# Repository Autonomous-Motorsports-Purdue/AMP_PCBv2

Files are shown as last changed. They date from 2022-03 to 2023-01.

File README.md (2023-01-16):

# AMP PCB version 2

This PCB attempts to refine the v1 PCB to strip away extraneous components and achieve the best minimal set of components needed for drive, steering, and braking control

## Features

| Name | Current Status | Notes |
|---|---|---|
| Foot switch | Working | Master enable for motor controller
| Forward throttle | Working | -
| Reverse throttle | Working | -
| Motor brake control | Untested | Primary braking system if working
| Emergency brake control | Working | Mechanical brake actuator
| Steering | Working | 0-100% PWM duty cycle control
| LoRa remote control | Partially tested | -
| Watchdog timer | Broken on Rev A | -
| Hardware serial port | Working | -

---

## Technical Information
- [Teensy 4.0 front pinout](docs/img/Teensy_40_Front_Pinout.png)
- [Teensy 4.0 rear pinout](docs/img/Teensy_40_Rear_Pinout.png)
- [Emergency brake controller truth table](docs/img/Brake_Control_Signals.png)

### Useful links
- [RC Low-pass Filter Design for PWM](http://sim.okawa-denshi.jp/en/PWMtool.php)
- [Software setup for Teensy with Arduino](https://www.pjrc.com/teensy/tutorial.html)

---

## Part Numbers
| Part Number | Description |
|---|---|
| [776164-1](https://www.digikey.com/en/products/detail/te-connectivity-deutsch-ict-connectors/776164-1/2183727) | AMPSEAL (main motor controller connector) 35-pin connector
| [770520-1](https://www.digikey.com/en/products/detail/te-connectivity-amp-connectors/770520-1/744981) | AMPSEAL crimps

---

## Miscellaneous notes (to check)

- Create documentation for connectors (especially motor controller connector)
- Create complete BOM for PCB

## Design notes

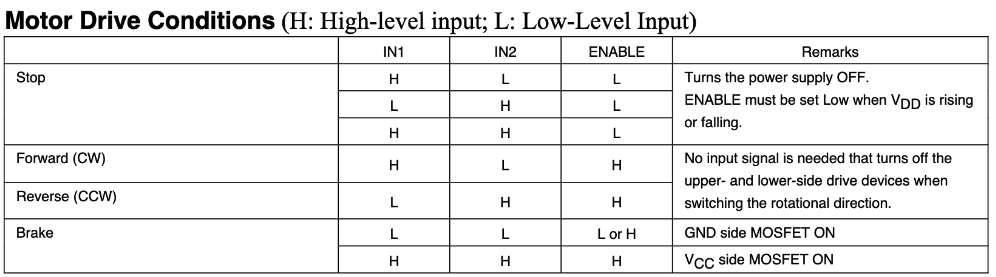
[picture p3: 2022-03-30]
docs/img/Brake_Control_Signals.png

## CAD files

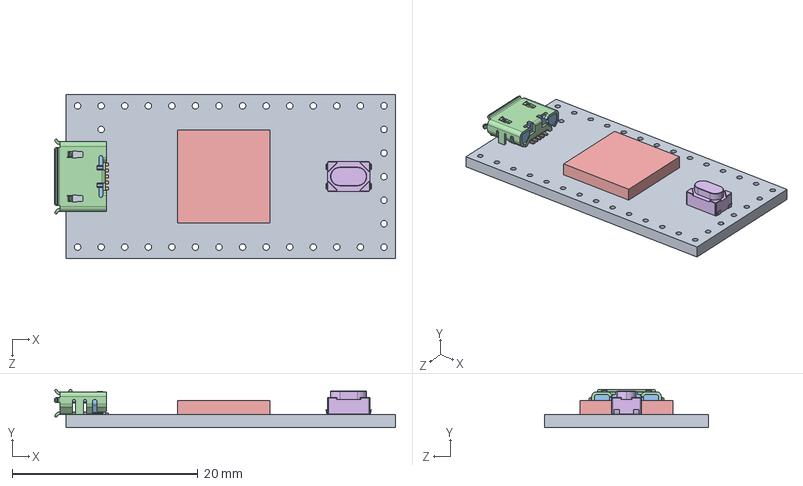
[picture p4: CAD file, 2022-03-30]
footprints/models/Teensy_4.0_Assembly.STEP
36.8 x 4.12 x 17.7 mm
Teensy_4.0_PCB
Micro USB-B Female 5Pin SMD
NXP iMXRT1062
SKRPACE010 v4

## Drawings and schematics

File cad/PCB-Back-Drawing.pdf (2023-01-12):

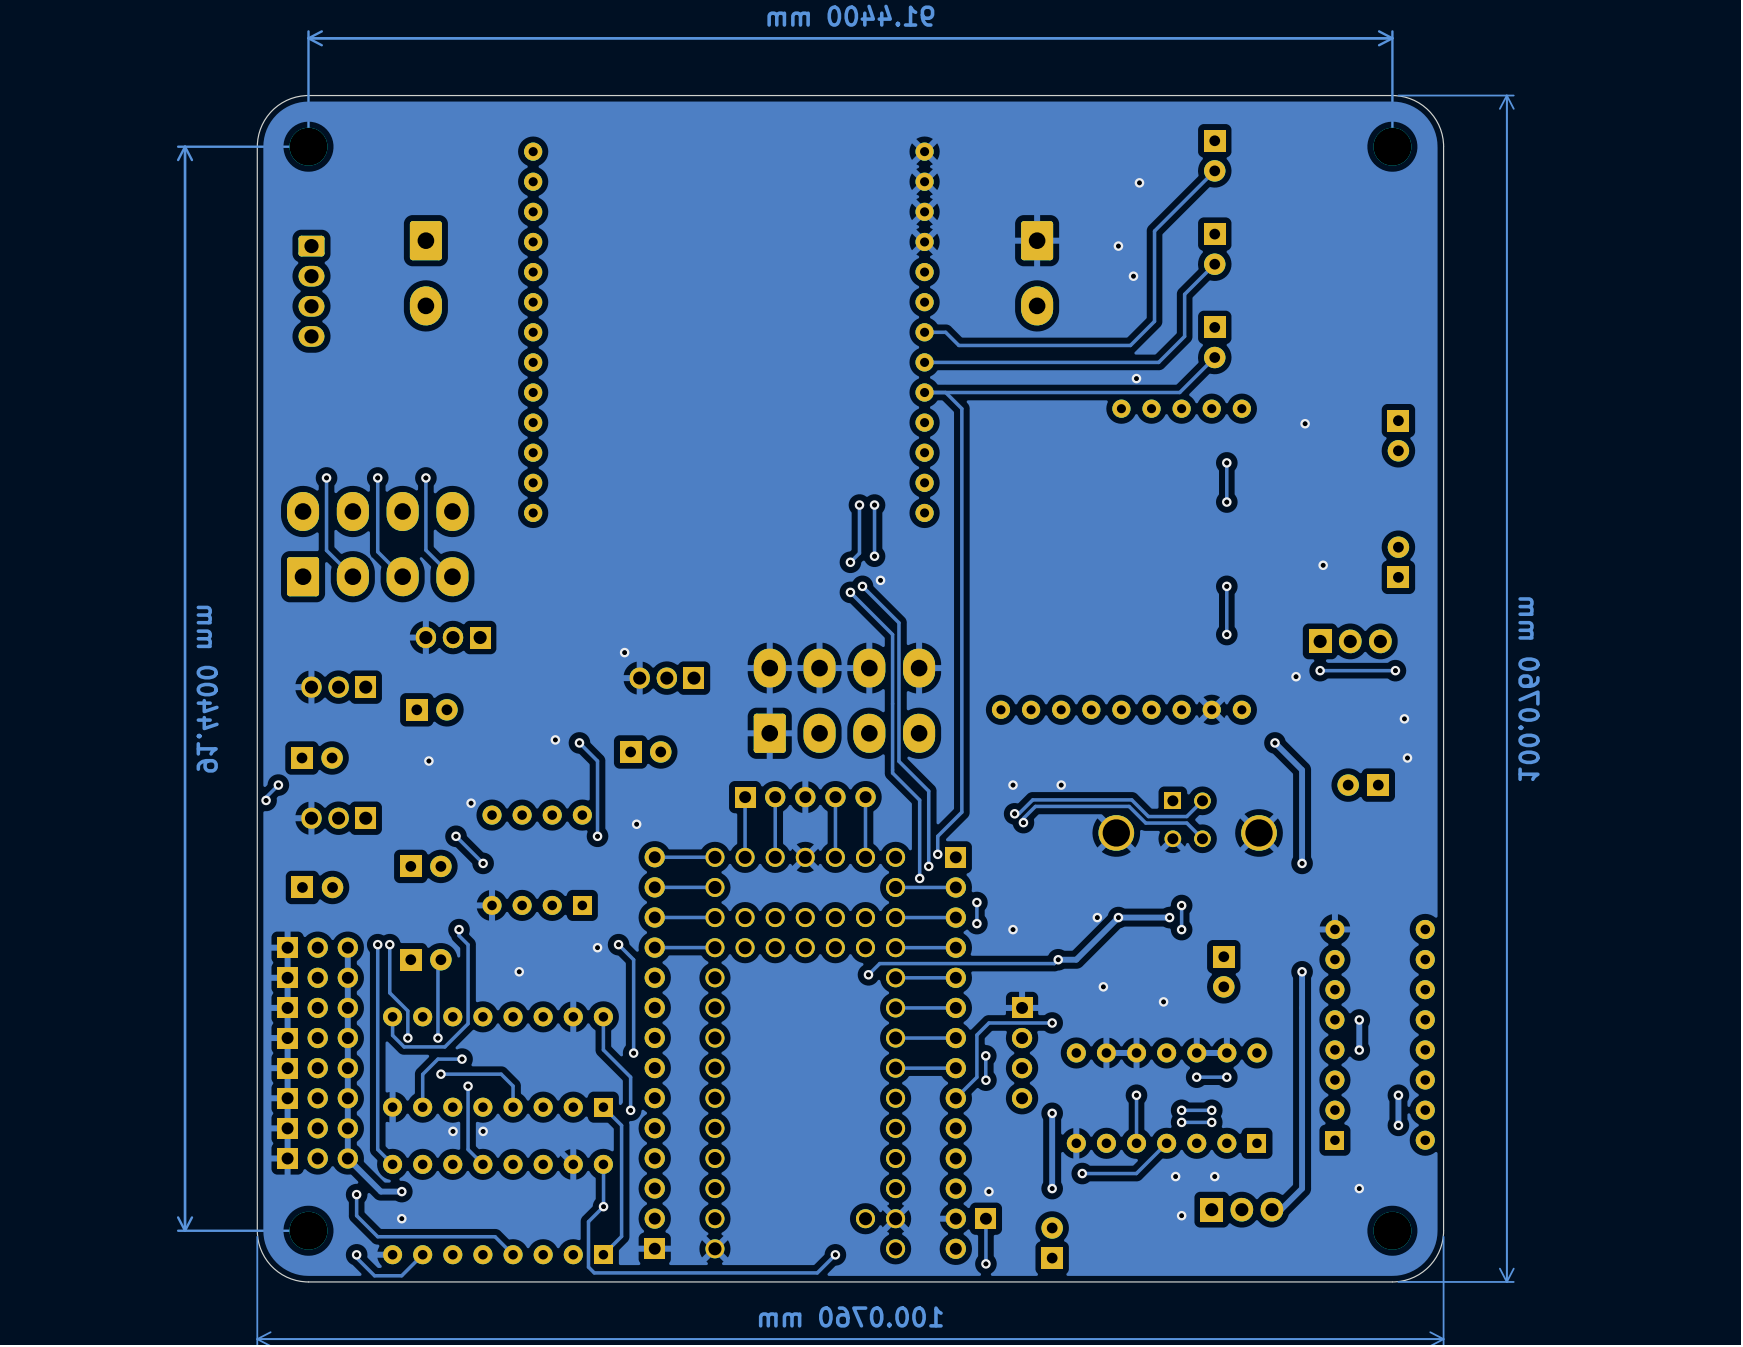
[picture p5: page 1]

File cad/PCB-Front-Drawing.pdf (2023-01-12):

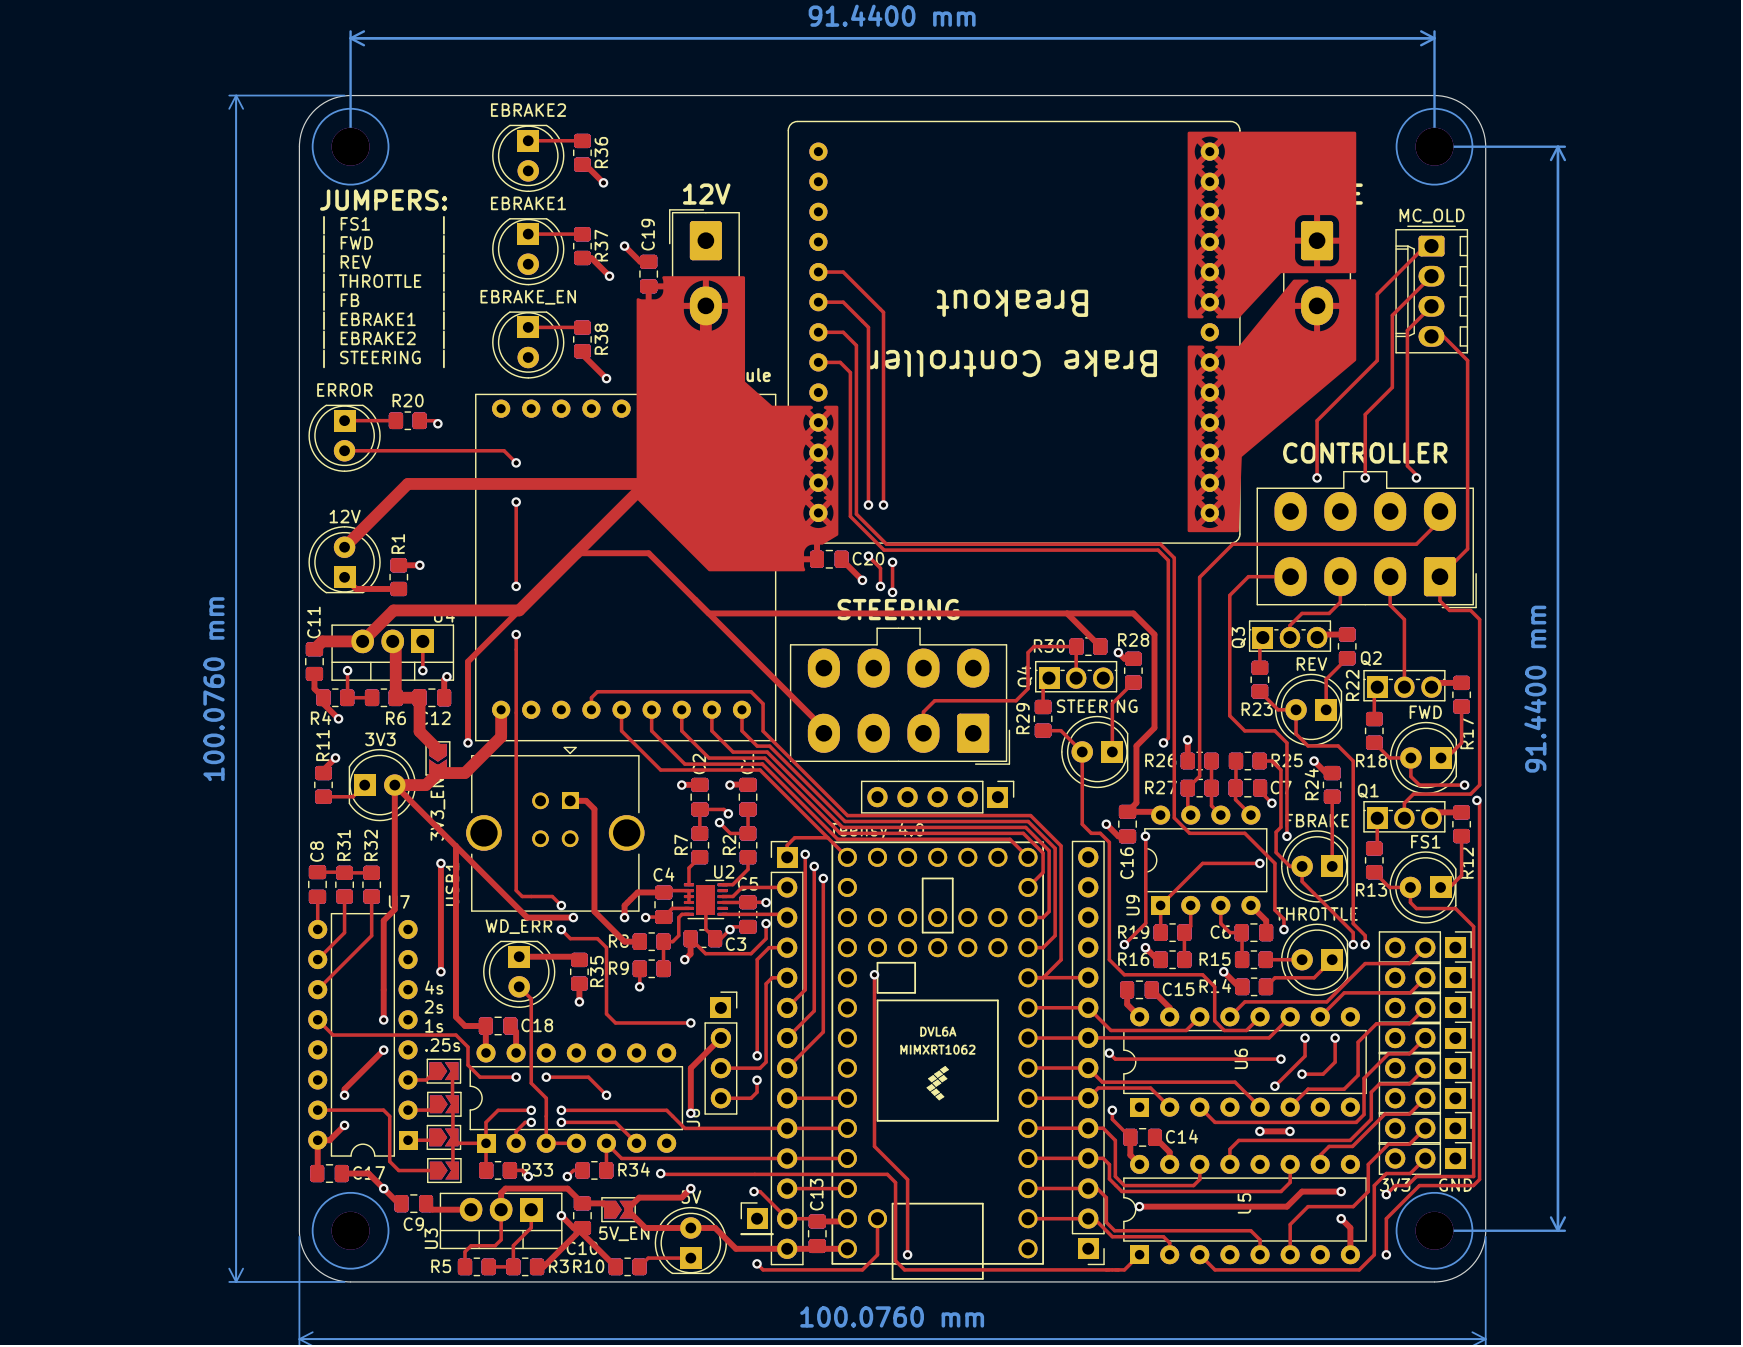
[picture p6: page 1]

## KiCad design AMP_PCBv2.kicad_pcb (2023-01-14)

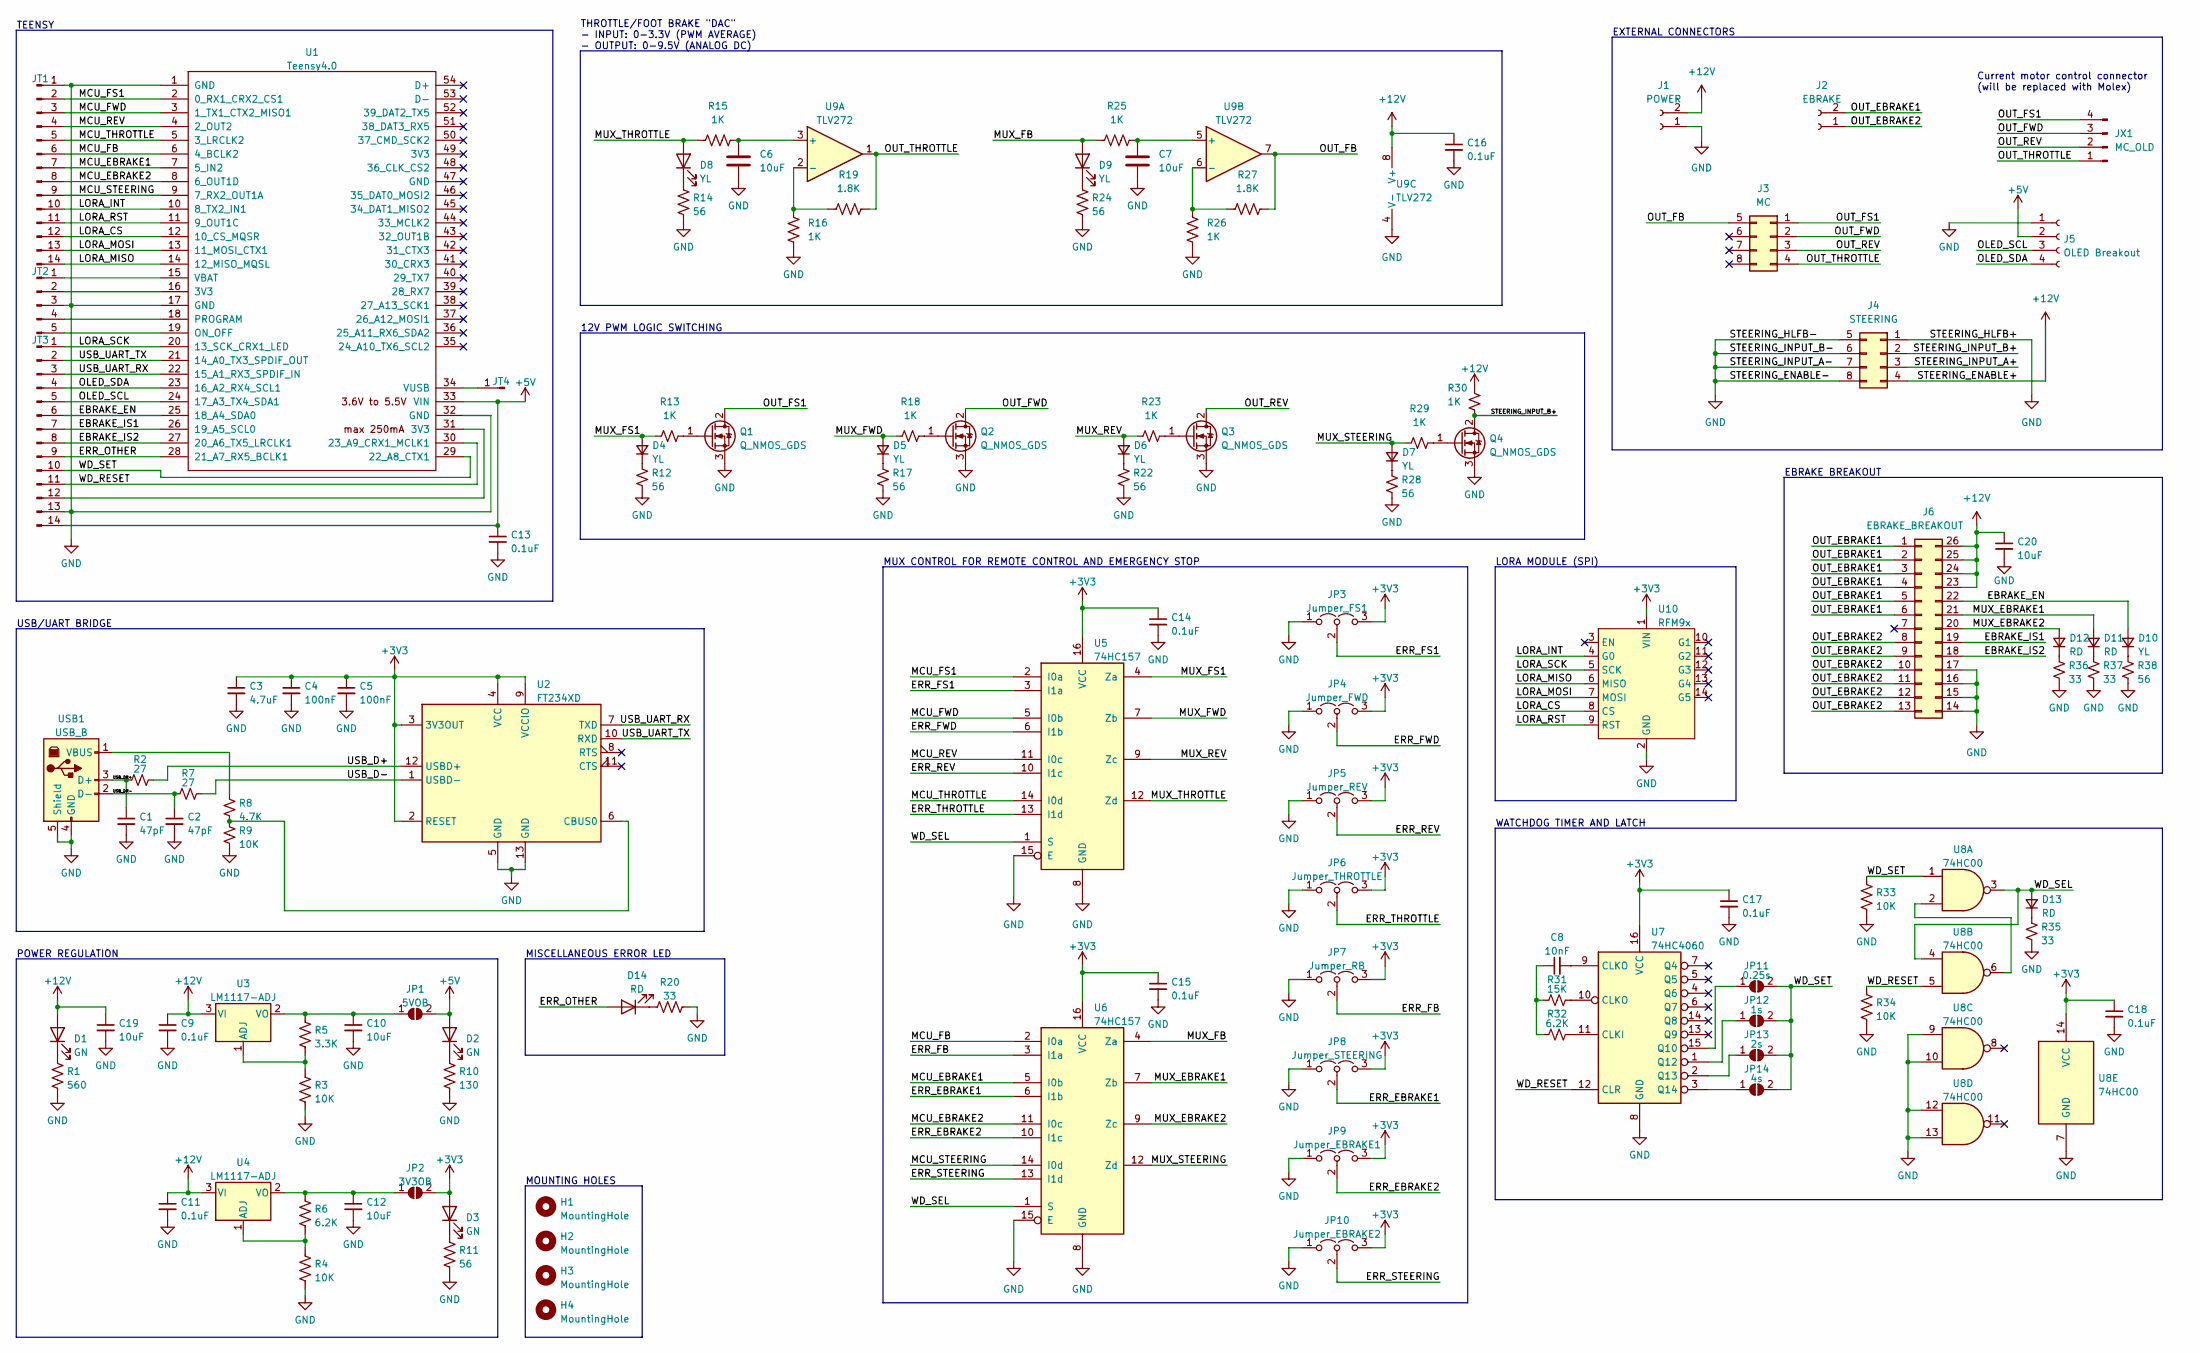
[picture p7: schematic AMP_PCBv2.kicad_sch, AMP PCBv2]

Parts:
C1, C2: 47pF; C_0805_2012Metric_Pad1.18x1.45mm_HandSolder
C3: 4.7uF; C_0805_2012Metric_Pad1.18x1.45mm_HandSolder
C4, C5: 100nF; C_0805_2012Metric_Pad1.18x1.45mm_HandSolder
C6, C7, C10, C12, C19, C20: 10uF; C_0805_2012Metric_Pad1.18x1.45mm_HandSolder
C8: 10nF; C_0805_2012Metric_Pad1.18x1.45mm_HandSolder
C9, C11, C13, C14, C15, C16, C17, C18: 0.1uF; C_0805_2012Metric_Pad1.18x1.45mm_HandSolder
D1, D2, D3: GN; LED_D5.0mm
D4, D5, D6, D7, D8, D9, D10: YL; LED_D5.0mm
D11, D12, D13, D14: RD; LED_D5.0mm
H1, H2, H3, H4: MountingHole; MountingHole_3.2mm_M3
J1: POWER; Molex_Mini-Fit_Jr_5566-02A_2x01_P4.20mm_Vertical
J2: EBRAKE; Molex_Mini-Fit_Jr_5566-02A_2x01_P4.20mm_Vertical
J3: MC; Molex_Mini-Fit_Jr_5566-08A_2x04_P4.20mm_Vertical
J4: STEERING; Molex_Mini-Fit_Jr_5566-08A_2x04_P4.20mm_Vertical
J5: OLED Breakout; PinSocket_1x04_P2.54mm_Vertical
J6: EBRAKE_BREAKOUT; AMP_Brake_Controller_Breakout
JP1: 5VOB; SolderJumper-2_P1.3mm_Open_TrianglePad1.0x1.5mm
JP2: 3V3OB; SolderJumper-2_P1.3mm_Open_TrianglePad1.0x1.5mm
JP3: Jumper_FS1; PinHeader_1x03_P2.54mm_Vertical
JP4: Jumper_FWD; PinHeader_1x03_P2.54mm_Vertical
JP5: Jumper_REV; PinHeader_1x03_P2.54mm_Vertical
JP6: Jumper_THROTTLE; PinHeader_1x03_P2.54mm_Vertical
JP7: Jumper_RB; PinHeader_1x03_P2.54mm_Vertical
JP8: Jumper_STEERING; PinHeader_1x03_P2.54mm_Vertical
JP9: Jumper_EBRAKE1; PinHeader_1x03_P2.54mm_Vertical
JP10: Jumper_EBRAKE2; PinHeader_1x03_P2.54mm_Vertical
JP11: 0.25s; SolderJumper-2_P1.3mm_Open_TrianglePad1.0x1.5mm
JP12: 1s; SolderJumper-2_P1.3mm_Open_TrianglePad1.0x1.5mm
JP13: 2s; SolderJumper-2_P1.3mm_Open_TrianglePad1.0x1.5mm
JP14: 4s; SolderJumper-2_P1.3mm_Open_TrianglePad1.0x1.5mm
JT1, JT3: Conn_01x14_Male; PinHeader_1x14_P2.54mm_Vertical
JT2: Conn_01x05_Male; PinHeader_1x05_P2.54mm_Vertical
JT4: Conn_01x01_Male; PinHeader_1x01_P2.54mm_Vertical
JX1: MC_OLD; Molex_KK-254_AE-6410-04A_1x04_P2.54mm_Vertical
Q1, Q2, Q3, Q4: Q_NMOS_GDS; TO-251-3_Vertical
R1: 560; R_0805_2012Metric_Pad1.20x1.40mm_HandSolder
R2, R7: 27; R_0805_2012Metric_Pad1.20x1.40mm_HandSolder
R3, R4, R9, R33, R34: 10K; R_0805_2012Metric_Pad1.20x1.40mm_HandSolder
R5: 3.3K; R_0805_2012Metric_Pad1.20x1.40mm_HandSolder
R6, R32: 6.2K; R_0805_2012Metric_Pad1.20x1.40mm_HandSolder
R8: 4.7K; R_0805_2012Metric_Pad1.20x1.40mm_HandSolder
R10: 130; R_0805_2012Metric_Pad1.20x1.40mm_HandSolder
R11, R12, R14, R17, R22, R24, R28, R38: 56; R_0805_2012Metric_Pad1.20x1.40mm_HandSolder
R13, R15, R16, R18, R23, R25, R26, R29, R30: 1K; R_0805_2012Metric_Pad1.20x1.40mm_HandSolder
R19, R27: 1.8K; R_0805_2012Metric_Pad1.20x1.40mm_HandSolder
R20, R35, R36, R37: 33; R_0805_2012Metric_Pad1.20x1.40mm_HandSolder
R31: 15K; R_0805_2012Metric_Pad1.20x1.40mm_HandSolder
U1: Teensy4.0; Teensy40
U2: FT234XD; DFN-12-1EP_3x3mm_P0.5mm_EP1.6x2.5mm
U3, U4: LM1117-ADJ; TO-220-3_Vertical
U5, U6: 74HC157; DIP-16_W7.62mm
U7: 74HC4060; DIP-16_W7.62mm
U8: 74HC00; DIP-14_W7.62mm
U9: TLV272; DIP-8_W7.62mm
U10: RFM9x; RFM9x_Adafruit
USB1: USB_B; USB_B_TE_5787834_Vertical

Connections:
+3V3: C3.1, C4.1, C5.1, C14.1, C15.1, C17.1, C18.1, D3.2 (A), JP2.2 (B), JP3.3 (B), JP4.3 (B), JP5.3 (B), JP6.3 (B), JP7.3 (B), JP8.3 (B), JP9.3 (B), JP10.3 (B), U2.2 (RESET), U2.3 (3V3OUT), U2.4 (VCC), U2.9 (VCCIO), U5.16 (VCC), U6.16 (VCC), U7.16 (VCC), U8.14 (VCC), U10.1 (VIN)
+5V: C13.1, D2.2 (A), J5.2, JP1.2 (B), JT3.14, U1.33 (VIN)
+12V: C9.1, C11.1, C16.1, C19.1, C20.1, D1.2 (A), J1.2, J4.4, J6.23, J6.24, J6.25, J6.26, R30.2, U3.3 (VI), U4.3 (VI), U9.8 (V+)
/EBRAKE_EN: D10.2 (A), J6.22, JT3.6, U1.25 (18_A4_SDA0)
/EBRAKE_IS1: J6.19, JT3.7, U1.26 (19_A5_SCL0)
/EBRAKE_IS2: J6.18, JT3.8, U1.27 (20_A6_TX5_LRCLK1)
/ERR_EBRAKE1: JP8.2 (C), U6.6 (I1b)
/ERR_EBRAKE2: JP9.2 (C), U6.10 (I1c)
/ERR_FB: JP7.2 (C), U6.3 (I1a)
/ERR_FS1: JP3.2 (C), U5.3 (I1a)
/ERR_FWD: JP4.2 (C), U5.6 (I1b)
/ERR_OTHER: D14.2 (A), JT3.9, U1.28 (21_A7_RX5_BCLK1)
/ERR_REV: JP5.2 (C), U5.10 (I1c)
/ERR_STEERING: JP10.2 (C), U6.13 (I1d)
/ERR_THROTTLE: JP6.2 (C), U5.13 (I1d)
/LORA_CS: JT1.12, U1.12 (10_CS_MQSR), U10.8 (CS)
/LORA_INT: JT1.10, U1.10 (8_TX2_IN1), U10.4 (G0)
/LORA_MISO: JT1.14, U1.14 (12_MISO_MQSL), U10.6 (MISO)
/LORA_MOSI: JT1.13, U1.13 (11_MOSI_CTX1), U10.7 (MOSI)
/LORA_RST: JT1.11, U1.11 (9_OUT1C), U10.9 (RST)
/LORA_SCK: JT3.1, U1.20 (13_SCK_CRX1_LED), U10.5 (SCK)
/MCU_EBRAKE1: JT1.7, U1.7 (5_IN2), U6.5 (I0b)
/MCU_EBRAKE2: JT1.8, U1.8 (6_OUT1D), U6.11 (I0c)
/MCU_FB: JT1.6, U1.6 (4_BCLK2), U6.2 (I0a)
/MCU_FS1: JT1.2, U1.2 (0_RX1_CRX2_CS1), U5.2 (I0a)
/MCU_FWD: JT1.3, U1.3 (1_TX1_CTX2_MISO1), U5.5 (I0b)
/MCU_REV: JT1.4, U1.4 (2_OUT2), U5.11 (I0c)
/MCU_STEERING: JT1.9, U1.9 (7_RX2_OUT1A), U6.14 (I0d)
/MCU_THROTTLE: JT1.5, U1.5 (3_LRCLK2), U5.14 (I0d)
/MUX_EBRAKE1: D11.2 (A), J6.21, U6.7 (Zb)
/MUX_EBRAKE2: D12.2 (A), J6.20, U6.9 (Zc)
/MUX_FB: D9.2 (A), R25.1, U6.4 (Za)
/MUX_FS1: D4.2 (A), R13.1, U5.4 (Za)
/MUX_FWD: D5.2 (A), R18.1, U5.7 (Zb)
/MUX_REV: D6.2 (A), R23.1, U5.9 (Zc)
/MUX_STEERING: D7.2 (A), R29.1, U6.12 (Zd)
/MUX_THROTTLE: D8.2 (A), R15.1, U5.12 (Zd)
/OLED_SCL: J5.3, JT3.5, U1.24 (17_A3_TX4_SDA1)
/OLED_SDA: J5.4, JT3.4, U1.23 (16_A2_RX4_SCL1)
/OUT_EBRAKE1: J2.2, J6.1, J6.2, J6.3, J6.4, J6.5, J6.6
/OUT_EBRAKE2: J2.1, J6.8, J6.9, J6.10, J6.11, J6.12, J6.13
/OUT_FB: J3.5, R27.2, U9.7
/OUT_FS1: J3.1, JX1.4, Q1.2 (D)
/OUT_FWD: J3.2, JX1.3, Q2.2 (D)
/OUT_REV: J3.3, JX1.2, Q3.2 (D)
/OUT_THROTTLE: J3.4, JX1.1, R19.2, U9.1
/STEERING_INPUT_A+: J4.3
/STEERING_INPUT_B+: J4.2, Q4.2 (D), R30.1
/USB_D+: R2.2, U2.12 (USBD+)
/USB_D-: R7.2, U2.1 (USBD-)
/USB_DR+: C1.1, R2.1, USB1.3 (D+)
/USB_DR-: C2.1, R7.1, USB1.2 (D-)
/USB_UART_RX: JT3.3, U1.22 (15_A1_RX3_SPDIF_IN), U2.7 (TXD)
/USB_UART_TX: JT3.2, U1.21 (14_A0_TX3_SPDIF_OUT), U2.10 (RXD)
/WD_RESET: JT3.11, R34.1, U1.30 (23_A9_CRX1_MCLK1), U7.12 (CLR), U8.5
/WD_SEL: D13.2 (A), U5.1 (S), U6.1 (S), U8.3, U8.4
/WD_SET: JP11.2 (B), JP12.2 (B), JP13.2 (B), JP14.2 (B), JT3.10, R33.1, U1.29 (22_A8_CTX1), U8.1
GND: C1.2, C2.2, C3.2, C4.2, C5.2, C6.2, C7.2, C9.2, C10.2, C11.2, C12.2, C13.2, C14.2, C15.2, C16.2, C17.2, C18.2, C19.2, C20.2, J1.1, J4.1, J4.5, J4.6, J4.7, J4.8, J5.1, J6.14, J6.15, J6.16, J6.17, JP3.1 (A), JP4.1 (A), JP5.1 (A), JP6.1 (A), JP7.1 (A), JP8.1 (A), JP9.1 (A), JP10.1 (A), JT1.1, JT2.3, JT3.13, Q1.3 (S), Q2.3 (S), Q3.3 (S), Q4.3 (S), R1.2, R3.1, R4.1, R9.2, R10.2, R11.2, R12.2, R14.2, R16.2, R17.2, R20.2, R22.2, R24.2, R26.2, R28.2, R33.2, R34.2, R35.2, R36.2, R37.2, R38.2, U1.1 (GND), U1.17 (GND), U1.32 (GND), U2.5 (GND), U2.13 (GND), U5.8 (GND), U5.15 (E), U6.8 (GND), U6.15 (E), U7.8 (GND), U8.7 (GND), U8.9, U8.10, U8.12, U8.13, U9.4 (V-), U10.2 (GND), USB1.4 (GND), USB1.5 (Shield)
unnamed: C6.1, R15.2, U9.3 (+)
unnamed: C7.1, R25.2, U9.5 (+)
unnamed: C8.1, R31.1, R32.1
unnamed: C8.2, U7.9 (CLKO)
unnamed: C10.1, JP1.1 (A), R5.1, U3.2 (VO)
unnamed: C12.1, JP2.1 (A), R6.1, U4.2 (VO)
unnamed: D1.1 (K), R1.1
unnamed: D2.1 (K), R10.1
unnamed: D3.1 (K), R11.1
unnamed: D4.1 (K), R12.1
unnamed: D5.1 (K), R17.1
unnamed: D6.1 (K), R22.1
unnamed: D7.1 (K), R28.1
unnamed: D8.1 (K), R14.1
unnamed: D9.1 (K), R24.1
unnamed: D10.1 (K), R38.1
unnamed: D11.1 (K), R37.1
unnamed: D12.1 (K), R36.1
unnamed: D13.1 (K), R35.1
unnamed: D14.1 (K), R20.1
unnamed: JP11.1 (A), U7.15 (Q10)
unnamed: JP12.1 (A), U7.1 (Q12)
unnamed: JP13.1 (A), U7.2 (Q13)
unnamed: JP14.1 (A), U7.3 (Q14)
unnamed: JT2.1, U1.15 (VBAT)
unnamed: JT2.2, U1.16 (3V3)
unnamed: JT2.4, U1.18 (PROGRAM)
unnamed: JT2.5, U1.19 (ON_OFF)
unnamed: JT3.12, U1.31 (3V3)
unnamed: JT4.1, U1.34 (VUSB)
unnamed: Q1.1 (G), R13.2
unnamed: Q2.1 (G), R18.2
unnamed: Q3.1 (G), R23.2
unnamed: Q4.1 (G), R29.2
unnamed: R3.2, R5.2, U3.1 (ADJ)
unnamed: R4.2, R6.2, U4.1 (ADJ)
unnamed: R8.1, USB1.1 (VBUS)
unnamed: R8.2, R9.1, U2.6 (CBUS0)
unnamed: R16.1, R19.1, U9.2 (-)
unnamed: R26.1, R27.1, U9.6 (-)
unnamed: R31.2, U7.10 (CLKO)
unnamed: R32.2, U7.11 (CLKI)
unnamed: U8.2, U8.6

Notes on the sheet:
EBRAKE BREAKOUT
MISCELLANEOUS ERROR LED
WATCHDOG TIMER AND LATCH
MOUNTING HOLES
POWER REGULATION
EXTERNAL CONNECTORS
THROTTLE/FOOT BRAKE "DAC" - INPUT: 0-3.3V (PWM AVERAGE) - OUTPUT: 0-9.5V (ANALOG DC)
12V PWM LOGIC SWITCHING
TEENSY
LORA MODULE (SPI)
USB/UART BRIDGE
Current motor control connector (will be replaced with Molex)
MUX CONTROL FOR REMOTE CONTROL AND EMERGENCY STOP

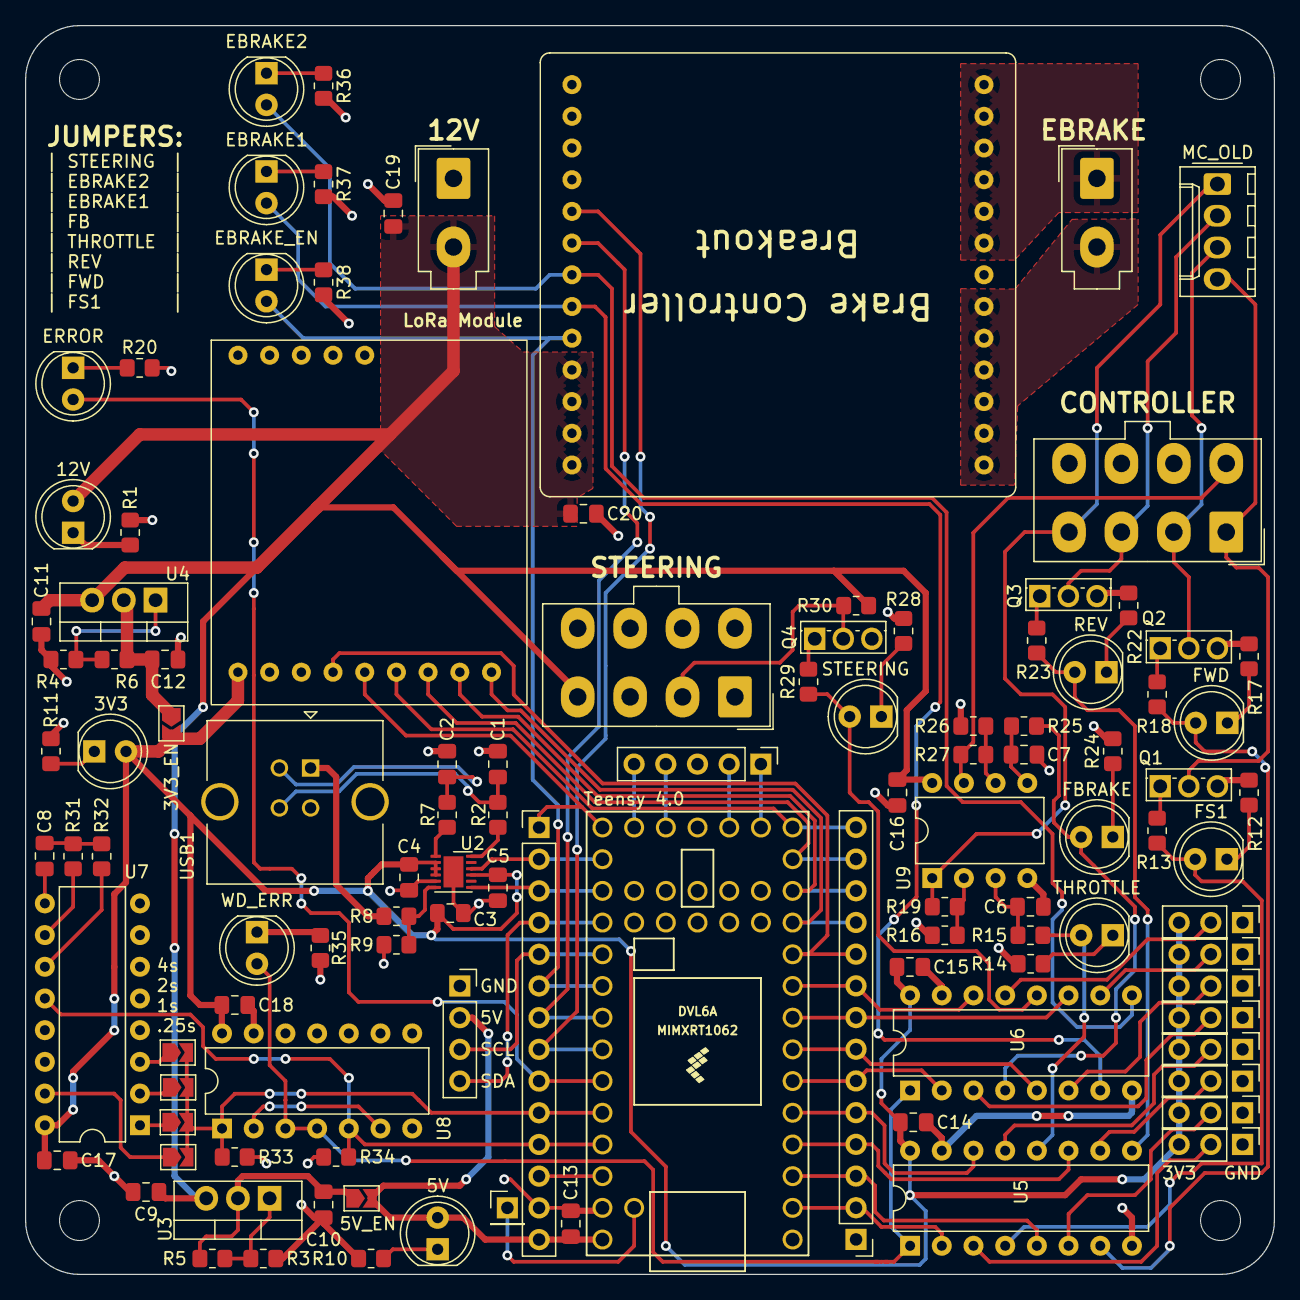
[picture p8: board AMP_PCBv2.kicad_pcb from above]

Board: 2 copper layers, 100.1 x 100.1 mm, 115 parts (0 on the bottom side), 100 nets.

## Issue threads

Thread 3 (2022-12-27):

Watchdog not 3.3V tolerant

benjamin-owen, 2022-12-27:
WD_SET and WD_RESET are connected to Teensy and they may be 5V logic lines.  Consider lowering watchdog timer Vcc to 3.3V or lowering logic lines to Teensy with voltage division.

benjamin-owen, 2022-12-27:
Going to change the counter and NAND gate chip Vcc to 3.3V, which should clamp the output voltage to safe levels.  The only things still running on 5V are the Teensy and OLED display power pin.

Closed 2022-12-27.

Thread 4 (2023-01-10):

D+/D- flipped

benjamin-owen, 2023-01-10:
The D+/D- connections between the external USB port and the FTDI chip are flipped.  Chip can communicate with computer if a cable is made with these connections flipped internally.

Closed 2023-01-12.

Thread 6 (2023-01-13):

Fix jumper label text

benjamin-owen, 2023-01-13:
The jumper text (top left of PCB) referring to the selectable jumpers (bottom right of PCB) does not line up correctly.  It appears to be reversed.

Closed 2023-01-14.

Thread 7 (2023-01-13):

Watchdog timer not working correctly

benjamin-owen, 2023-01-13:
The watchdog timer turns on and off at periodic intervals.  Consider checking in breadboard.  Output signals may be inverted causing issues with SR latch.

benjamin-owen, 2023-01-14:
Also consider increasing interval time, 4 second jumper appears to be closer to 2.

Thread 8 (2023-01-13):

LDO temperature

benjamin-owen, 2023-01-13:
Even idling, LDO temperature (especially the 3V3 regulator) is getting very hot.  Consider adding fan header, beefier heatsink, or replacing with switching regulator to avoid issues under load.

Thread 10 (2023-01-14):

Remove old motor controller connector

benjamin-owen, 2023-01-14:
Only needed once motor controller wiring is changed.  Remove the 4 pin fan header connector thing once converted to 4x2 molex connector.

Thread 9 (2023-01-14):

Add OLED connector labels

benjamin-owen, 2023-01-14:
It may be nice to label the pins for the OLED screen breakout to make sure the connections are correct.

Closed 2023-01-14.

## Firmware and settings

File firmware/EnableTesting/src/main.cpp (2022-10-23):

#include <Arduino.h>

#define FS1 2
#define FWD 3
#define REV 4

#define STR 7
#define THR 10

void set_idle()
{
    digitalWrite(FS1, LOW);
    //    digitalWrite(KS1, LOW);
    digitalWrite(FWD, LOW);
    digitalWrite(REV, LOW);
}

void set_enabled()
{
    digitalWrite(FS1, HIGH);
    delay(1000);
    digitalWrite(REV, LOW);
    //    digitalWrite(KS1, HIGH);
    digitalWrite(FWD, HIGH);
}


void setup() {
  Serial.begin(9600);
  pinMode(FS1, OUTPUT);
  pinMode(FWD, OUTPUT);
  pinMode(REV, OUTPUT);
  pinMode(STR, OUTPUT);
  pinMode(THR, OUTPUT);

  set_idle();
  Serial.println("idle");
  delay(2000);
  set_enabled();
  Serial.println("enabled");
  delay(2000);
}

void loop() {
  // loops through steering values and for every complete loop
  // it will iterate the throttle value by 10:
  for(int j = 0; j < 256; j+=20)
  {
      analogWrite(THR, j);
      delay(2000);
      Serial.println(j);
    // for(int i = 1000; i <= 5000; i+= 100)
    // {
    //   tone(STR, i); //   pin, freq
    // }
  }
}

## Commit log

2022-03-31 added bare bones schematic
    [AMP_PCBv2.kicad_sch]
2022-04-06 Add MOSFET gate resistors, other misc cleanup
    [AMP_PCBv2.kicad_sch]
2022-10-23 Update steering MOSFET configuration
    [AMP_PCBv2.kicad_sch]
2022-10-31 Add mux chain, foot brake amplifier; schematic cleanup
    [AMP_PCBv2.kicad_sch]
2022-11-05 Add wire-board connectors
    [AMP_PCBv2.kicad_sch]
2022-11-05 Update op-amp PN and add e-brake breakout
    [AMP_PCBv2.kicad_sch]
2022-11-05 Remove logo schematic designator
    [AMP_PCBv2.kicad_sch]
2022-11-06 Add AMPSEAL connector part number
2022-12-09 Change DAC op-amp gain
    [AMP_PCBv2.kicad_sch]
2022-12-23 Add watchdog timer, USB/UART, power regulators, finish pin connections and add annotations
    [AMP_PCBv2.kicad_sch]
2022-12-23 Add brake controller breakout footprint
2022-12-23 Add decoupling capacitors and assign footprints
    [AMP_PCBv2.kicad_sch]
2022-12-23 Change OLED screen footprint
    [AMP_PCBv2.kicad_sch]
2022-12-23 Route PCB
    [AMP_PCBv2.kicad_pcb]
2022-12-23 Add logo and label text
    [AMP_PCBv2.kicad_pcb]
2022-12-24 Route differential pair for USB connection
    [AMP_PCBv2.kicad_pcb, AMP_PCBv2.kicad_sch]
2022-12-26 Add LoRa module and extra decoupling capacitors
    [AMP_PCBv2.kicad_sch]
2022-12-26 Route new PCB (with LoRa)
    [AMP_PCBv2.kicad_pcb, AMP_PCBv2.kicad_sch]
2022-12-26 Add 3D models
    [AMP_PCBv2.kicad_pcb]
2022-12-26 Update library structure
    [AMP_PCBv2.kicad_pcb]
2022-12-26 Add extra error LED
    [AMP_PCBv2.kicad_pcb, AMP_PCBv2.kicad_sch]
2022-12-26 Schematic clean up
    [AMP_PCBv2.kicad_sch]
2022-12-27 Fix #3
    [AMP_PCBv2.kicad_pcb, AMP_PCBv2.kicad_sch]
2022-12-27 Generate gerber files for Revision A
    [AMP_PCBv2-B_Cu.gbl, AMP_PCBv2-B_Mask.gbs, AMP_PCBv2-B_Paste.gbp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]
2023-01-10 Add Teensy pinout images
2023-01-12 Fix D+/D- flipped #4
    [AMP_PCBv2.kicad_pcb, AMP_PCBv2.kicad_sch]
2023-01-12 Increase thickness of some traces to 0.3mm
    [AMP_PCBv2.kicad_pcb]
2023-01-12 Classify project as Revision B
    [AMP_PCBv2.kicad_pcb, AMP_PCBv2.kicad_sch]
2023-01-12 Add PCB drawing files
    [AMP_PCBv2.kicad_pcb]
2023-01-14 Add OLED connector labels #9
    [AMP_PCBv2.kicad_pcb]
2023-01-14 Fix jumper label text #6
    [AMP_PCBv2.kicad_pcb]
2023-01-14 Change PCB info text to be relative to KiCad file
    [AMP_PCBv2.kicad_pcb, AMP_PCBv2.kicad_sch]
